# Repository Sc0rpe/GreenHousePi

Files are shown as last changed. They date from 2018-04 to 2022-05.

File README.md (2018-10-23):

# GreenHousePi
This Project is from four students of the [Technische Universität Bergakademie Freiberg](https://tu-freiberg.de) in germany.
It was created for the subject "application of information and automizationsystems".
The goal of this project is to build an autonomous greenhouse with different features using a raspberry pi.

Desired features:
* Tracking of Temperature, Humidity, Soil Moisture and Light Intensity
* Ability to open the roof for cooling and ventilation
* Turning on the lights if the available light intensity is too low
* Ventilate with the Fan if the humidity is too high
* Water if the soil moisture is too low
* Ability to be operated over a backend
* Displaying values over a LCD-Screen

# Installation
1. Download the latest raspbian image from https://www.raspberrypi.org/downloads/raspbian/
    (light image because of performance recommended)
2. Install it
3. Run
	`sudo raspi-config` 
    and enable the I2C Interface under advanced options
4. Dowload the ghpi-library, therefore run 
    `git clone https://github.com/Sc0rpe/GreenHousePi`
5. If you connected your devices on different pins than we did change the defines in the file
    `ghpi.cc` 
6. Go into the folder `ghpi` and run
    `make main`
    Output will be a file `ghpi.o`
7. You can run it with
    `sudo ./ghpi.o`
8. If you want it to start after boot automaticaly add
    `./path/to/ghpi.o`
    to the end of the file /etc/rc.local
9. Also you can copy the binary into the folder `/usr/local/bin` so you can run it from everywhere by typing `sudo ghpi.o`

# Setting up the Webinterface
1. Run 
    ```
    sudo apt-get update
    sudo apt-get upgrade
    ```
2. Install the `lighttpd` Webserver
    ```
    sudo apt-get install lighttpd
    ```
3. Install `php7.0`
    ```
    sudo apt-get install php7.0
    ```
4. Activate the FastCGI Modul for php and restart the server
    ```
    sudo lighty-enable-mod fastcgi
    sudo lighty-enable-mod fastcgi-php
    sudo service lighttpd force-reload
    ```
5. Add the user `www-data` to the sudoers so it can run the software modules.
    Therefore run `sudo visudo` and add the line `www-data ALL=(ALL) NOPASSWD: ALL` to it.
    Exit with `[CTRL] + [X]`, confirm with `[Y]` and press `[ENTER]`.
6. Go into the folder `GreenHousePi/ghpi/webscripts` and run:
    ```
    make
    sudo make install
    ```
    This will compile the modules and copy them, the html and php files into the root directory of the webserver. By default this is `/var/www/html` for lighttpd. If this is different for you, you have to copy them manually or change the concerning lines in the makefile.

# Class Layout
For the full UML class diagram please have a look at `Documentation/UML/GreenHousePi-ClassDiagram.png` or open the UML XML file on [Draw.io](https://draw.io)
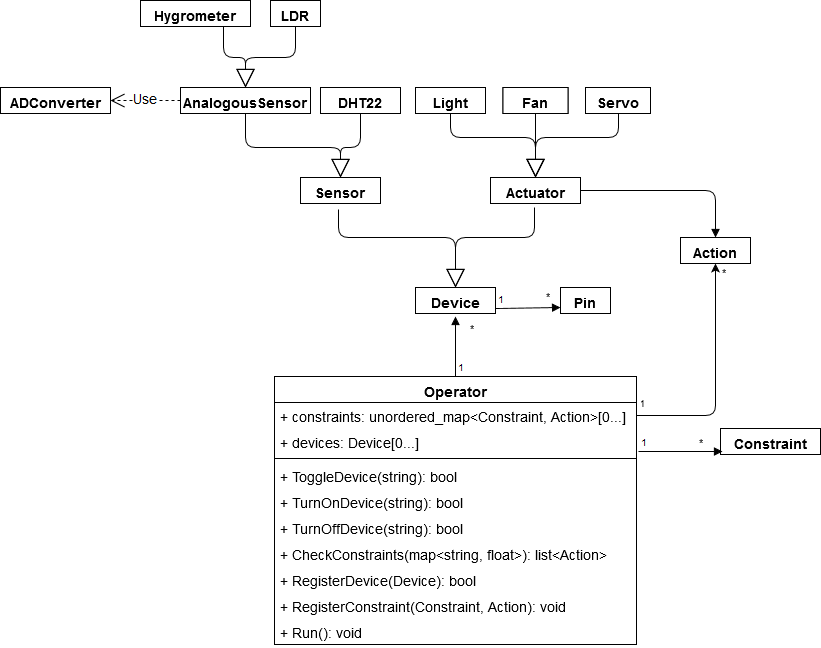
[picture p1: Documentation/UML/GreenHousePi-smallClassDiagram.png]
UML Class Diagram


# Cycle Schedule
This is what a cycle is doing. A cycle is one call of the Operater::Run function.
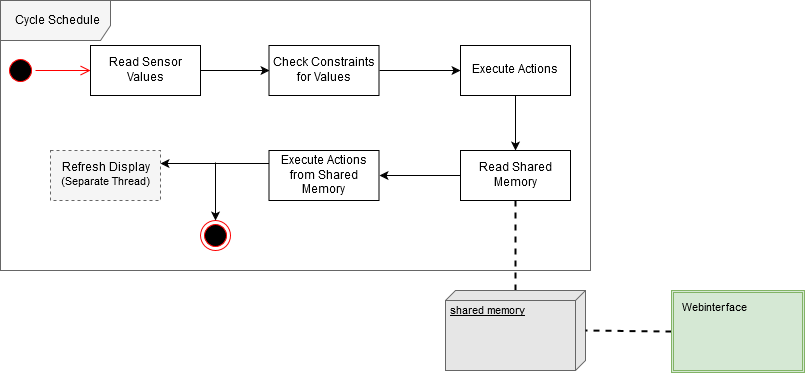
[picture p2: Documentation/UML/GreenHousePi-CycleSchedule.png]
Cycle schedule


# Adding your own Sensor
1. Create a new class and inherit from `ghpi::Sensor`
2. Override the `Run` and `get_values` function
4. Create an instance of your class, create some instances of Pin for your device and register them using the `RegisterPin()` function
5. Register your instance to the Operator using `RegisterDevice()`
6. For better understanding have look at the `dht22.cpp` file
7. Don't forget to add your newly created file to the makefile for the main target, otherwise it won't be linked if your run `make main`

# Adding your own Actuator
1. Create a new class and inherit from `ghpi::Actuator`
2. Override `TurnOn` `TurnOff` `Toggle` and if needed the `Run` function 
3. Create instances of `ghpi::Action` and register the actions your Actuator can execute by using `RegisterAction()`
4. Connect them by registering them with a Constraint on the operater using `RegisterConstraint`
5. Don't forget to add your newly created file to the makefile for the main target, otherwise it won't be linked if your run `make main`

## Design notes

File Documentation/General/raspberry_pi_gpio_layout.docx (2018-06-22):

Platine 3V | 3v3 | 5V | Platine 5V
Display SDA | 8 | 5V
Display SCL | 9 | GND
| 7 | 15
Platine GND | GND | 16 | RC2
LED_B | 0 | 1 | PWM
LED_G | 2 | GND
LED_R | 3 | 4 | RC3
| 3v3 | 5
ADC MOSI | 12 | GND | RC1
ADC MISO | 13 | 6 | DHT22 Data Pin
ADC CLK | 14 | 10 | ADC CS
Levelshifter GND | GND | 11

## GreenHousePi Pin Layout

Using wiringPi numbering!

RC stands for relay channel

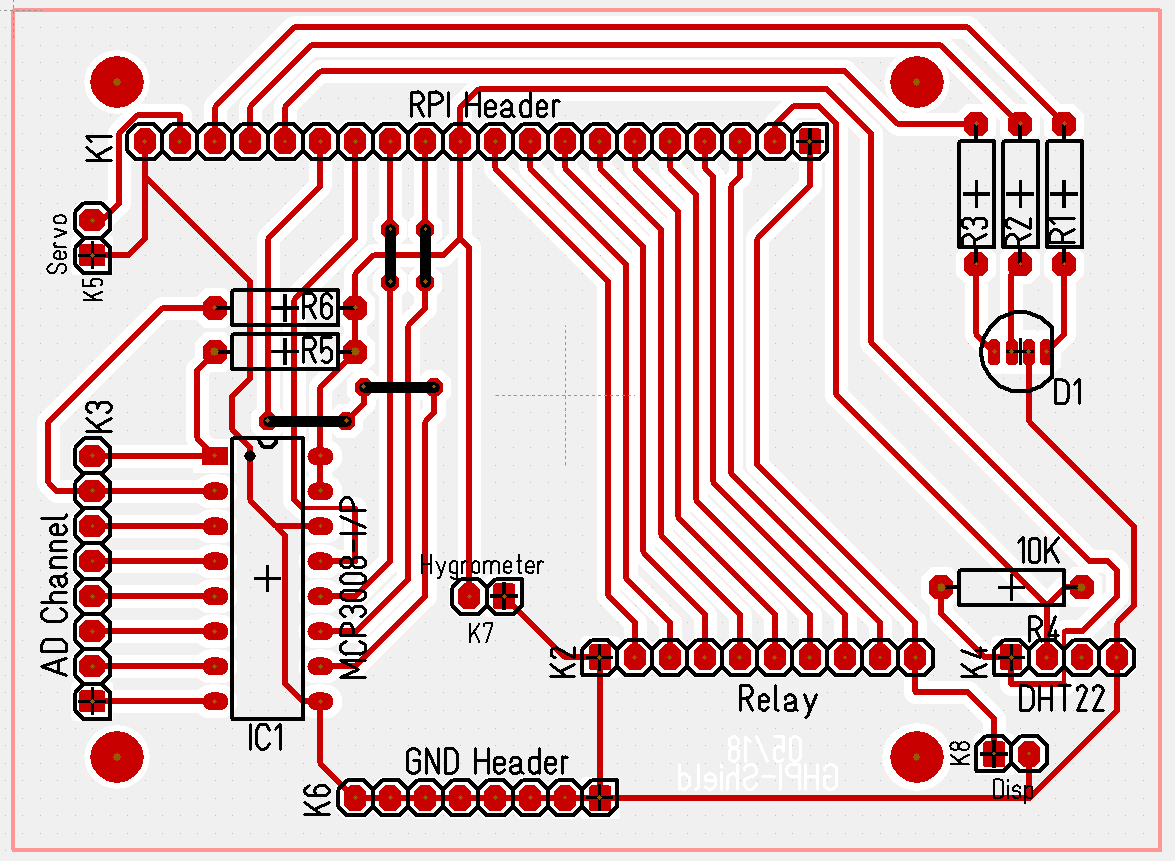
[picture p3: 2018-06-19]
Documentation/Images/ghpi_shield_pcb_layout_diagram.PNG

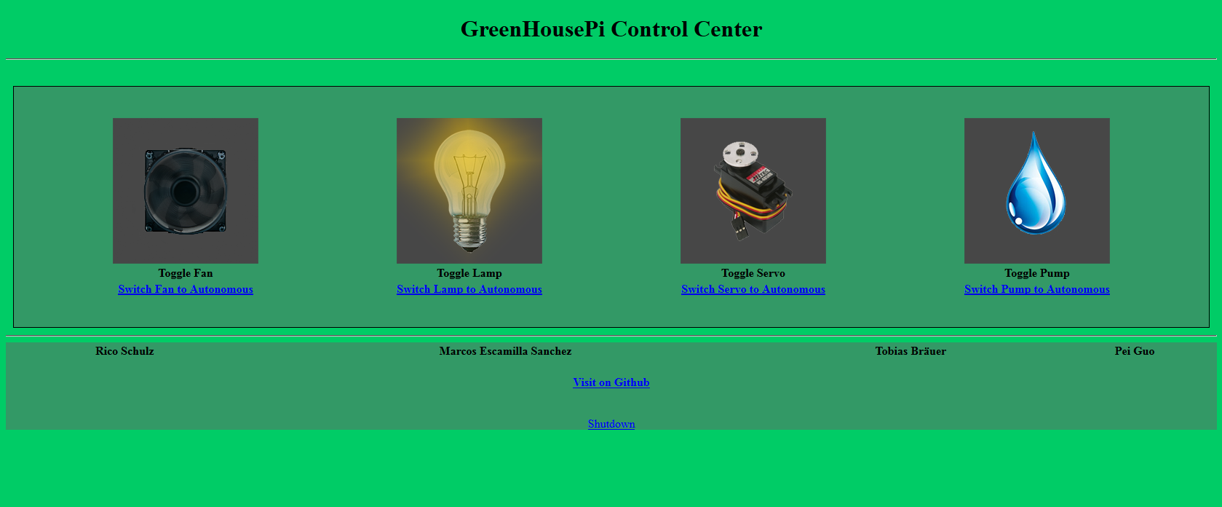
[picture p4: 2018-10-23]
Documentation/Images/webinterface.PNG

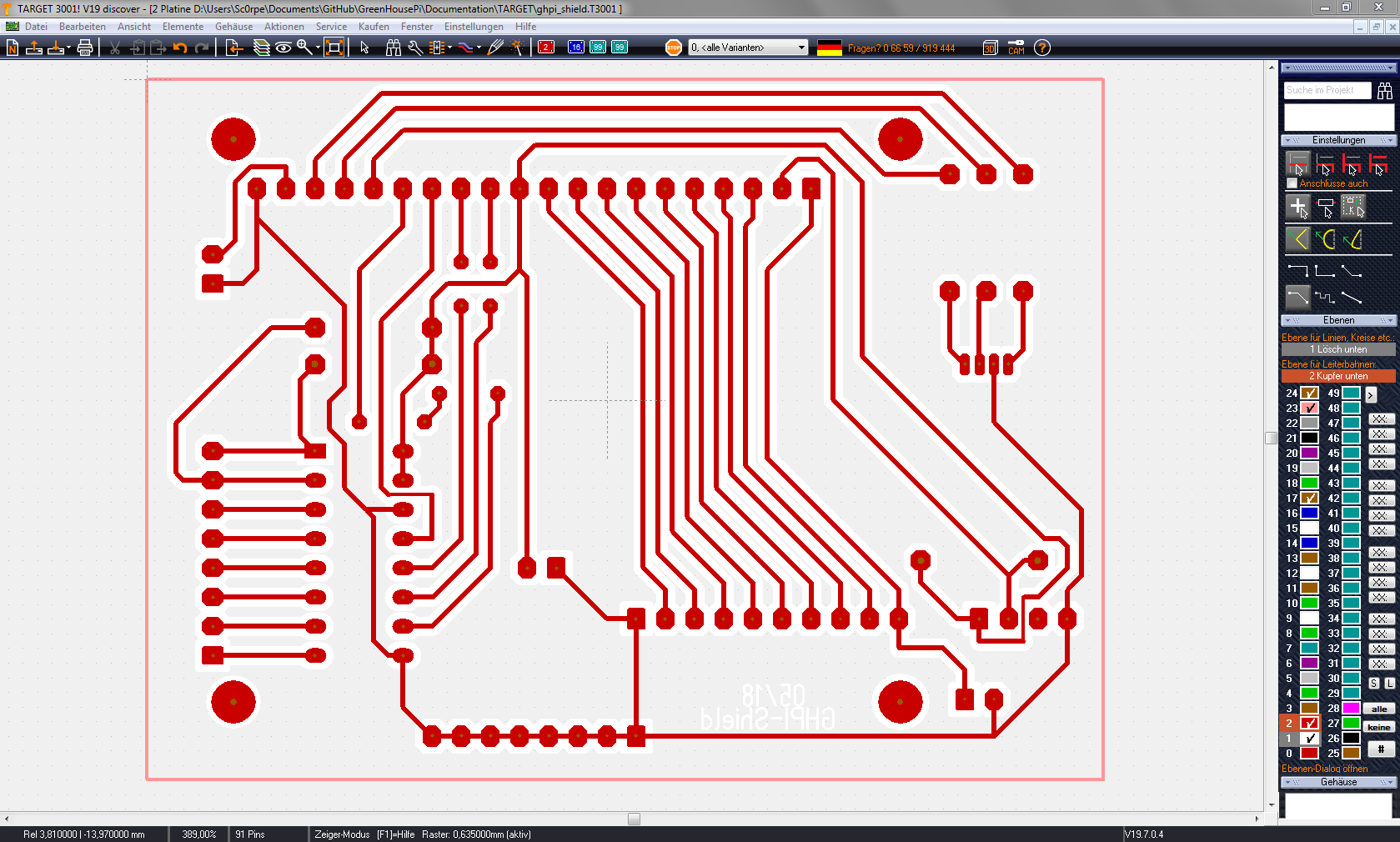
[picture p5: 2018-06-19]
Documentation/Images/target_screenshot1.PNG

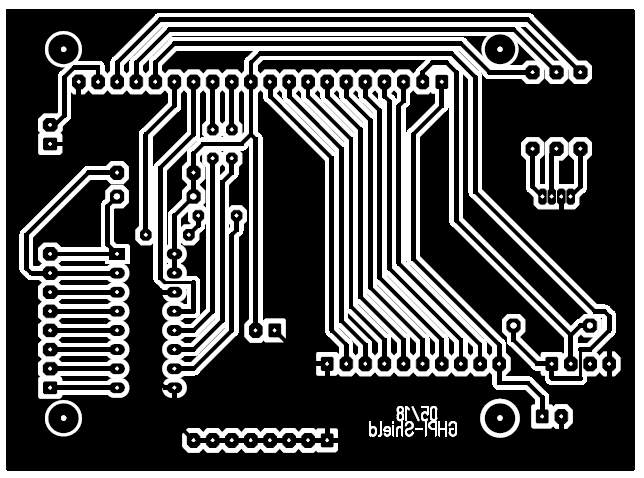
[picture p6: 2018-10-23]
Documentation/Images/illumination_mask.PNG

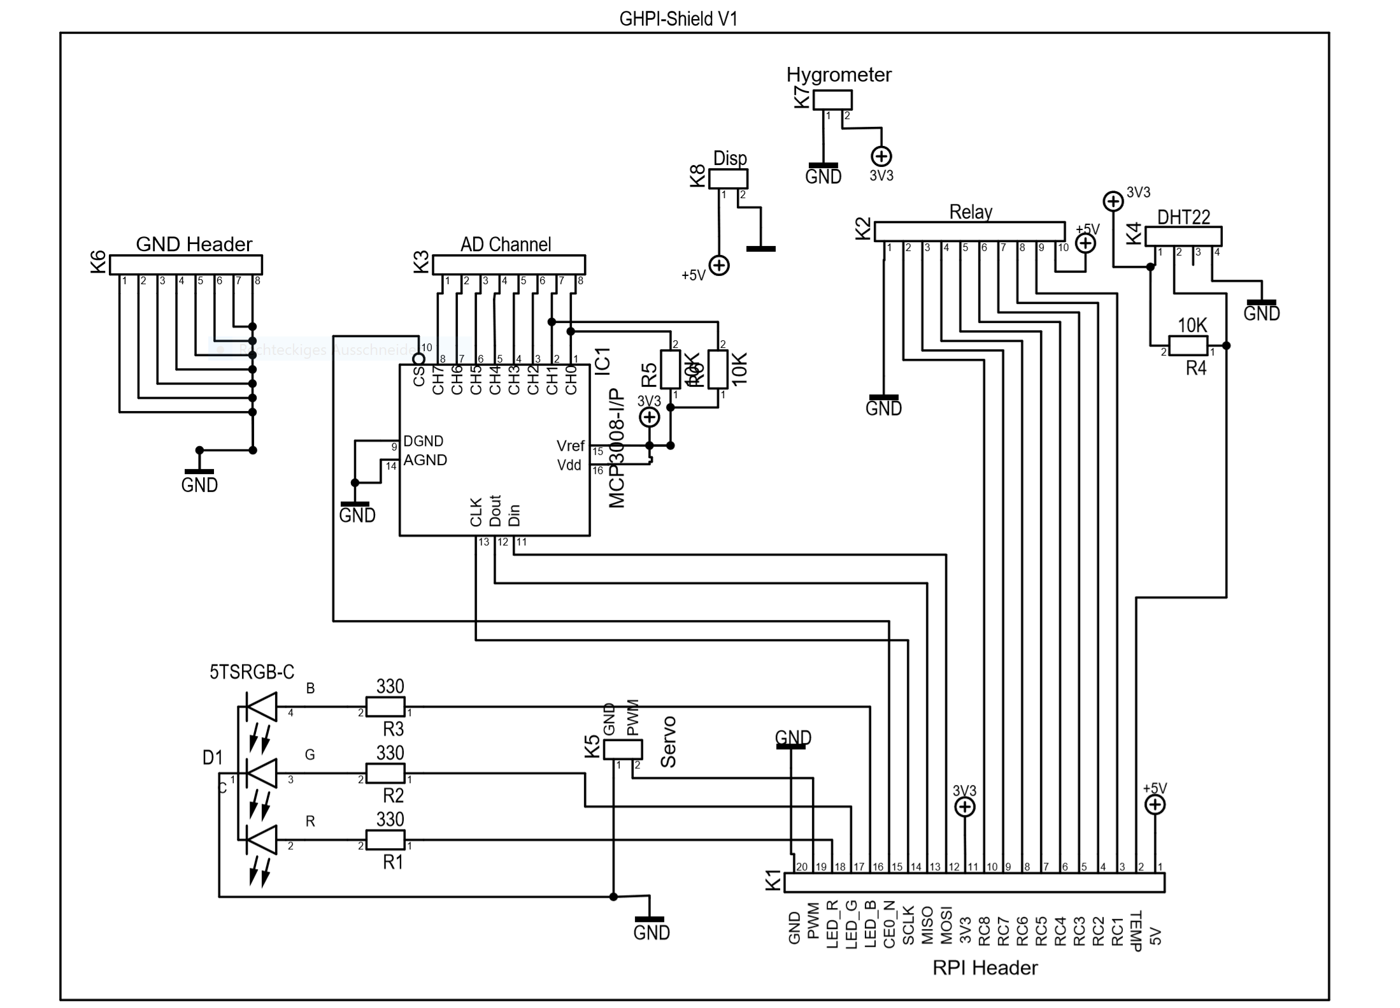
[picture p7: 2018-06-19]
Documentation/Images/ghpi_shield_sch.PNG

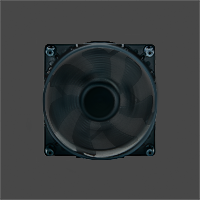
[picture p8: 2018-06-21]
ghpi/webscripts/images/fanON.png

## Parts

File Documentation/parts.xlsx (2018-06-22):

GreenHouse Pi Components
Component | Amount | Price per piece | Price
DHT22 Temperature and Humidity Sensor (https://www.amazon.de/AZDelivery-Temperatur-Luftfeuchtigkeitssensor-Arduino-Raspberry/dp/B06XF4TNT9) | 1 | 6.79 € | 6.79 €
Servo motor (https://www.amazon.de/Digital-Kuman-Rotating-Helicopter-Airplane/dp/B072V7RRF1?s=ce-de) | 1 | 19.29 € | 19.29 €
1000 uF Kondensator (https://www.amazon.de/Marken-100%C2%B5F-Kondensator-Elektrolytkondensator-Capacitor/dp/B014I7WV7A) | 1 | 0.58 € | 0.58 €
Raspberry Pi 2 Model B (https://www.amazon.de/Raspberry-Pi-quad-core-Cortex-A7-compatibility/dp/B00T2U7R7I?s=ce-de) | 0 | 37.99 € | 0.00 €
Power Supply for Motor (https://www.amazon.de/gp/product/B002E4WNWI/ref=oh_aui_detailpage_o00_s00?ie=UTF8&psc=1) | 1 | 12.00 € | 12.00 €
AD DA Wandler MCP3008 (https://www.amazon.de/gp/product/B005T6BA4K/ref=oh_aui_detailpage_o02_s00?ie=UTF8&psc=1) | 1 | 6.00 € | 6.00 €
8-Channel Relay (https://www.amazon.de/gp/product/B00AEIDWXK/ref=oh_aui_detailpage_o04_s00?ie=UTF8&psc=1) | 1 | 3.35 € | 3.35 €
photoconductive cell (https://www.amazon.de/gp/product/B00JGFF6HM/ref=oh_aui_detailpage_o04_s00?ie=UTF8&psc=1) | 2 | 0.18 € | 0.35 €
330 Ohm Resistor for the photoconductive cell | 3 | 0.00 € | 0.00 €
Power Supply Water pump 12V (https://www.amazon.de/Sunix-Netzadapter-100-240V-Transformatoren-Stromversorgung/dp/B074W2ZLDR) | 1 | 8.99 € | 8.99 €
Connector Strip (https://www.amazon.de/gp/product/B00GJP1JIM/ref=oh_aui_detailpage_o00_s00?ie=UTF8&psc=1) | 1 | 8.49 € | 8.49 €
Water Pump (https://www.amazon.de/TSSS-Wasserpumpe-Submersible-Gartenteich-Unterhaltung/dp/B01I9BN3CI) | 1 | 9.99 € | 9.99 €
Light (https://www.amazon.de/gp/product/B0183MDDZ0/ref=oh_aui_detailpage_o00_s00?ie=UTF8&psc=1) | 1 | 7.99 € | 7.99 €
Other stuff | 1 | 25.00 € | 25.00 €
Sum |  |  | 108.82 €
Price per Person |  |  | 27.20 €

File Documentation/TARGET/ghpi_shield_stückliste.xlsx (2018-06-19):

; Datum=09.Juni.2018 11:31
; Autor=Rico Schulz
Pos | Name | Wert | Gehäuse
1 | D1 | 5TSRGB-C | LED_5mm_RGB_4Pol
2 | IC1 | MCP3008-I/P | DIL16
3 | K1 | RPI Header | Stiftleiste_1x20_G_2,54
4 | K2 | Relay | Stiftleiste_1x10_G_2,54
5 | K3 | AD Channel | Stiftleiste_1x08_G_2,54
6 | K4 | DHT22 | Stiftleiste_1x04_G_2,54
7 | K5 | Servo | Stiftleiste_1x02_G_2,54
8 | K6 | GND Header | Stiftleiste_1x08_G_2,54
9 | K7 | Hygrometer | Stiftleiste_1x02_G_2,54
10 | K8 | Disp | Stiftleiste_1x02_G_2,54
11 | R1 | 330 Ohm | 0207_MET
12 | R2 | 330 Ohm | 0207_MET
13 | R3 | 330 Ohm | 0207_MET
14 | R4 | 10 kOhm | 0207_MET
15 | R5 | 10 kOhm | 0207_MET
16 | R6 | 10 kOhm | 0207_MET

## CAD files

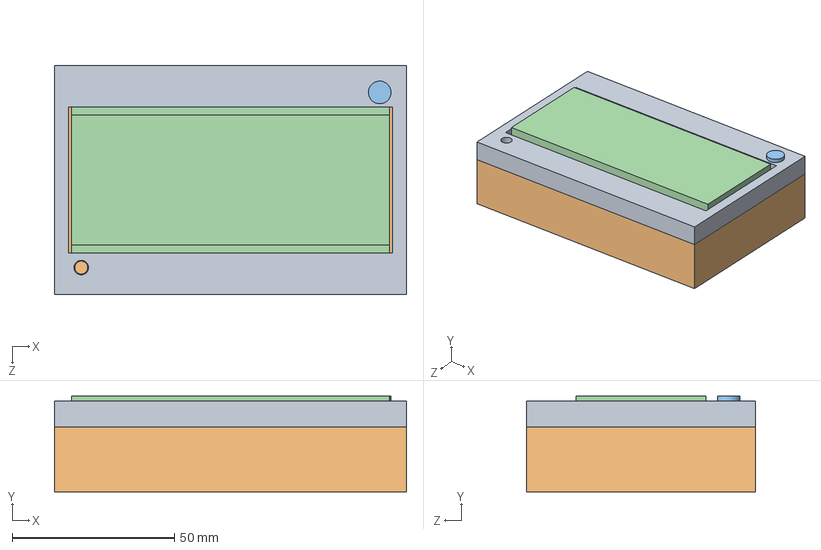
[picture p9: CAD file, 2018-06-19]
Documentation/SolidWorks CAD/Display/Displaycase.SLDASM
108.5 x 29.5 x 70.5 mm
Upper_case
Lower_case

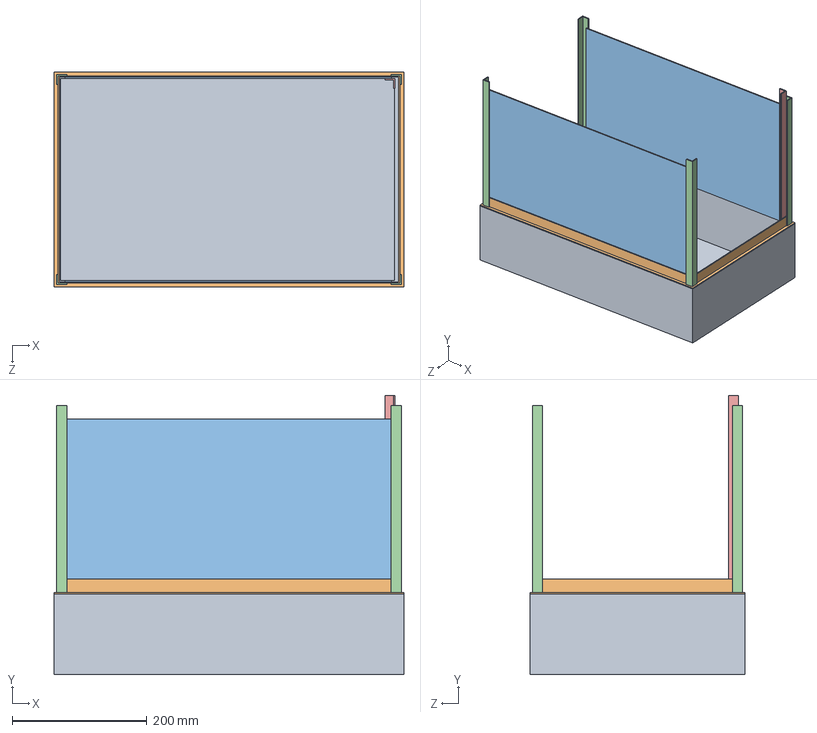
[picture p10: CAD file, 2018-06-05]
Documentation/SolidWorks CAD/Baugruppe.SLDASM
520.0 x 415.0 x 320.0 mm
bottom
bottom_frame
glass1 x 2
top_frame_out1 x 4
top_frame1

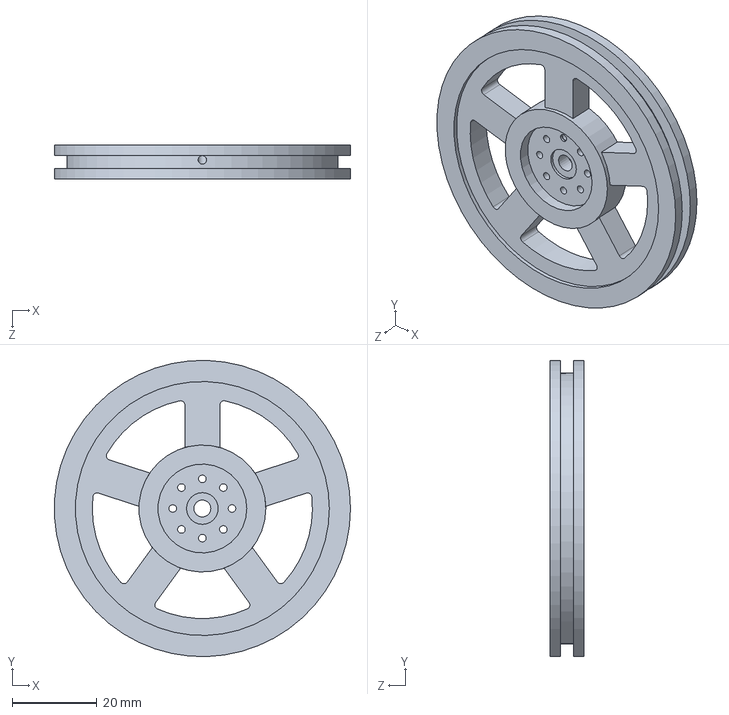
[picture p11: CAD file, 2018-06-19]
Documentation/SolidWorks CAD/Cable_Wheel/Cable_Wheel.SLDPRT
69.9 x 70.0 x 8.00 mm

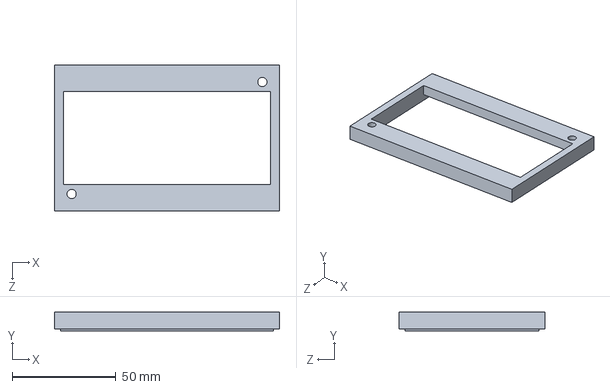
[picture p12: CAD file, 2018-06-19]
Documentation/SolidWorks CAD/Display/3D-Print/Upper_case.SLDPRT
108.5 x 9.00 x 70.5 mm

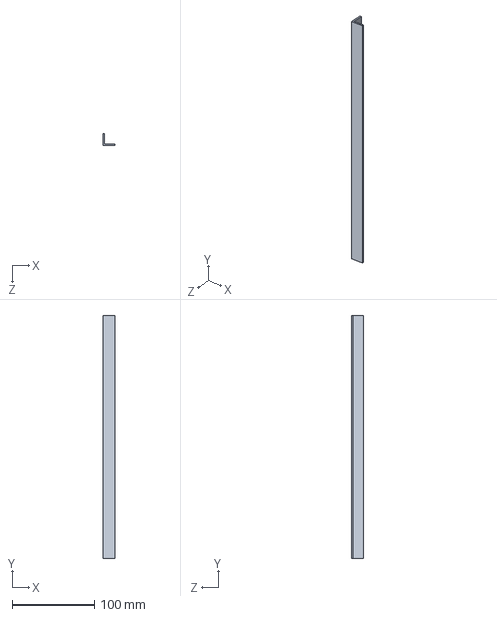
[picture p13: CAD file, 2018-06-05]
Documentation/SolidWorks CAD/top_frame1.SLDPRT
15.0 x 295.0 x 15.0 mm

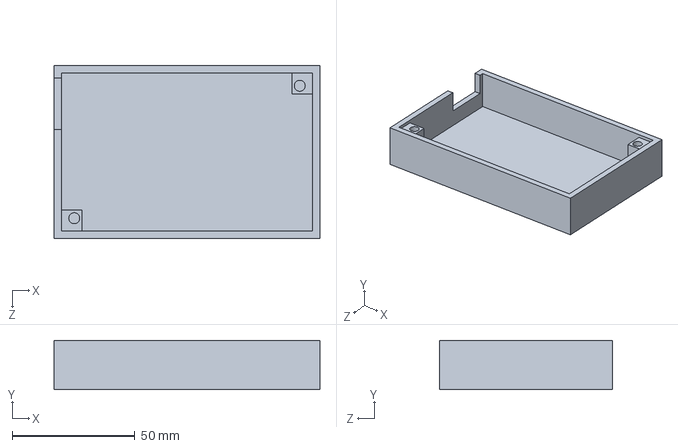
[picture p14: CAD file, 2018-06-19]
Documentation/SolidWorks CAD/Display/3D-Print/Lower_case.SLDPRT
108.5 x 20.0 x 70.5 mm

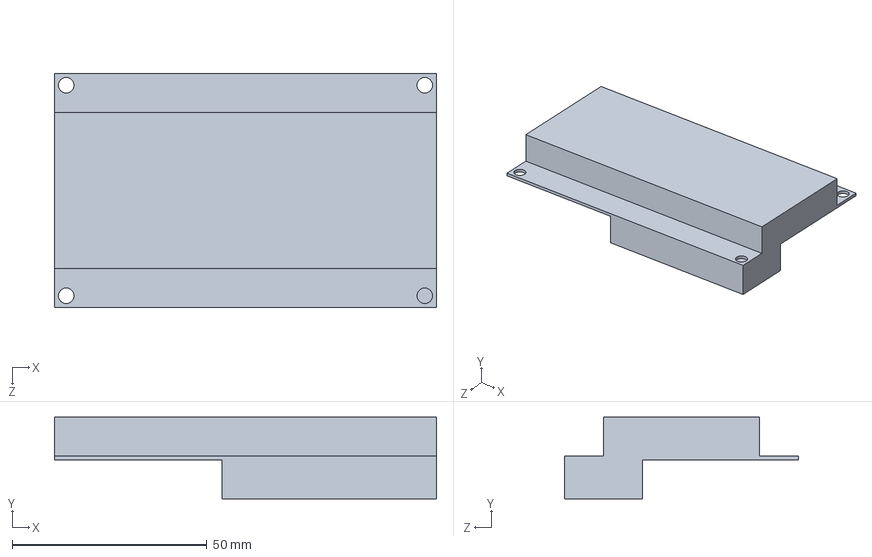
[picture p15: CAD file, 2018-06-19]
Documentation/SolidWorks CAD/Display/Display.SLDPRT
98.0 x 21.0 x 60.0 mm

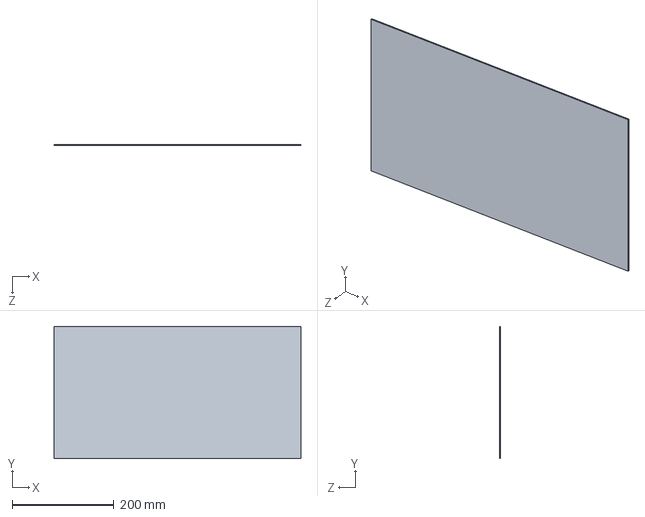
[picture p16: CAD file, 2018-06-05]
Documentation/SolidWorks CAD/glass1.SLDPRT
485.0 x 260.0 x 2.00 mm

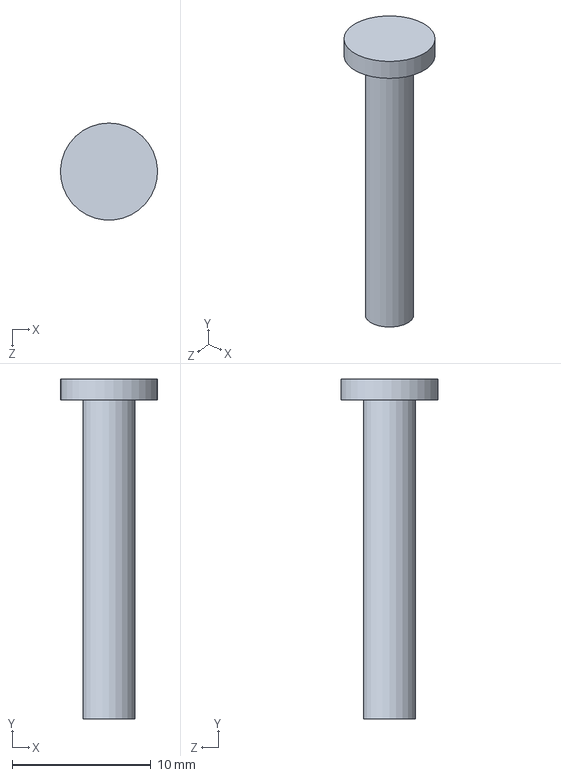
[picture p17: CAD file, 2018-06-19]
Documentation/SolidWorks CAD/Display/3D-Print/case_pin.SLDPRT
6.99 x 24.5 x 6.98 mm

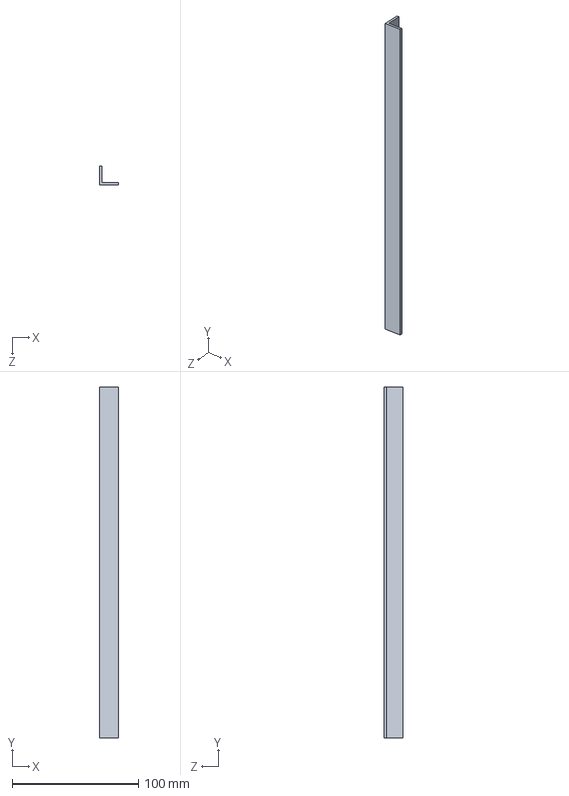
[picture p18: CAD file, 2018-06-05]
Documentation/SolidWorks CAD/top_frame_out1.SLDPRT
15.0 x 278.0 x 15.0 mm

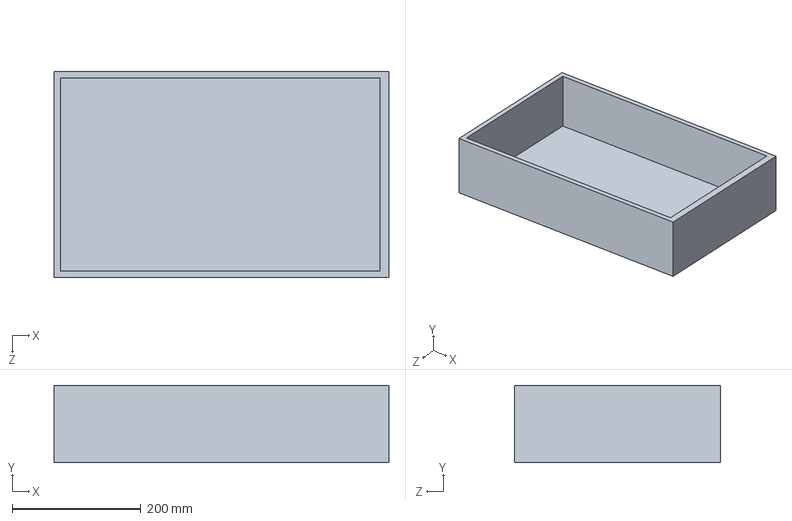
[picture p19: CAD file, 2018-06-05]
Documentation/SolidWorks CAD/bottom.SLDPRT
520.0 x 120.0 x 320.0 mm

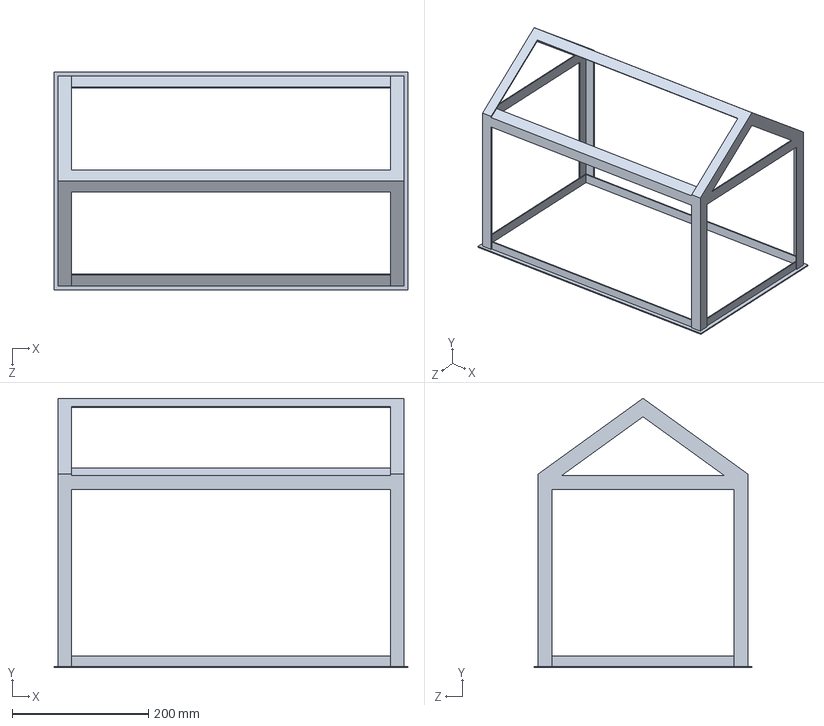
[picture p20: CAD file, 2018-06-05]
Documentation/SolidWorks CAD/top.SLDPRT
520.0 x 395.8 x 320.0 mm

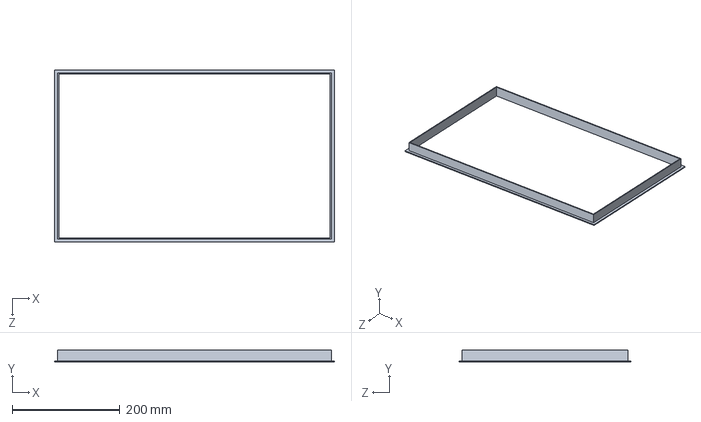
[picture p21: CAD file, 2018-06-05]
Documentation/SolidWorks CAD/bottom_frame.SLDPRT
520.0 x 22.0 x 320.0 mm

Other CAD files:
Documentation/SolidWorks CAD/Cable_Wheel/Cable_Wheel.STL
Documentation/SolidWorks CAD/Display/3D-Print/Lower_case.STL
Documentation/SolidWorks CAD/Display/3D-Print/Upper_case.STL
Documentation/SolidWorks CAD/Display/3D-Print/case_pin.STL
Documentation/SolidWorks CAD/greenhousepi_sketch.SLDDRW

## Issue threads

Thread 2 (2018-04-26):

Used GPIO Pins are not exportet on startup

Sc0rpe, 2018-04-26:
GPIOs are first exportet when the script wants to use it. This leads to a not working backend. If a device for instance the fan was not used by the script yet the backend functions will not switch its status.

Sc0rpe, 2018-04-30:
added pin_exporter.cpp
Let this be called after startup. Put this in /etc/rc.local to do this.
Not yet tested!

Sc0rpe, 2018-05-04:
Tested. Is working!

Closed 2018-05-04.

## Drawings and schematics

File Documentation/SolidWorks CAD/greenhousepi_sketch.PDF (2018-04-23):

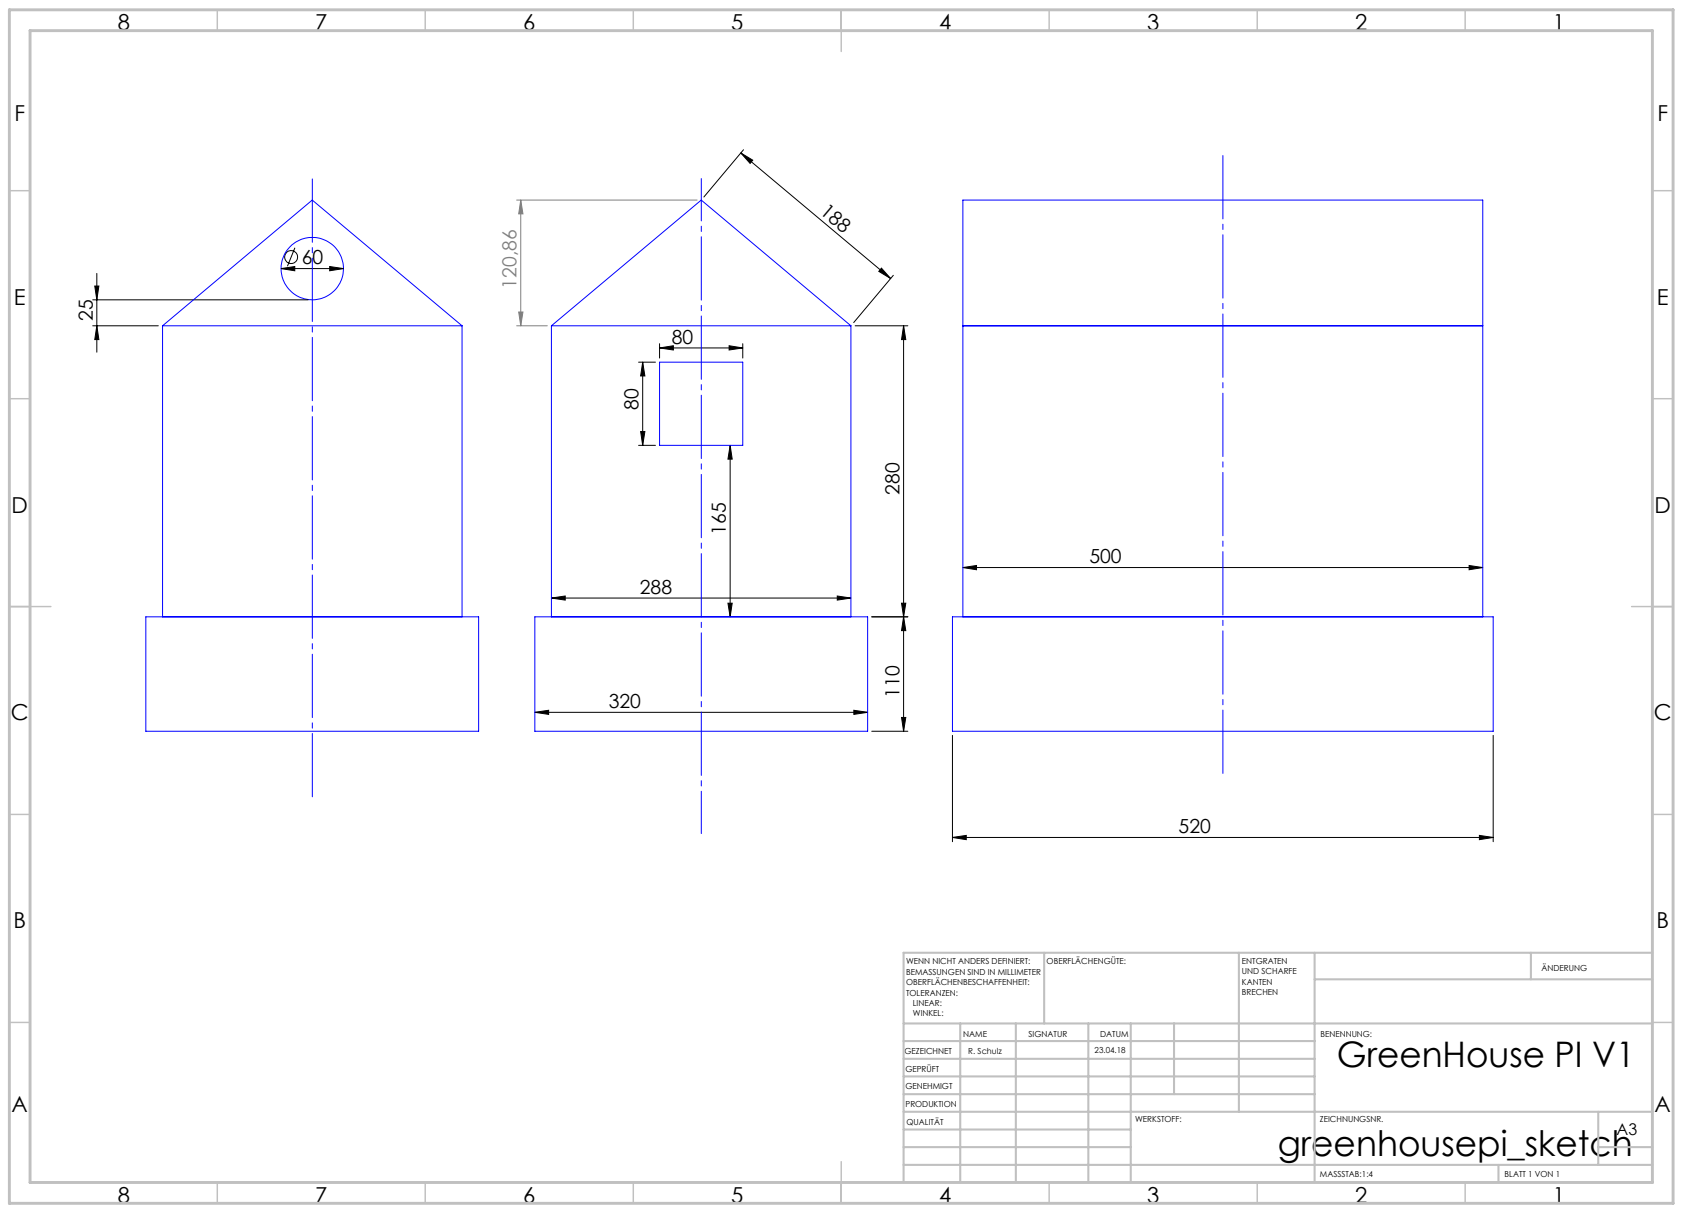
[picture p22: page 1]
MASSSTAB:1:4; BLATT 1 VON 1; UND SCHARFE; WENN NICHT ANDERS DEFINIERT:; OBERFLÄCHENGÜTE:

BEMASSUNGEN SIND IN MILLIMETER
OBERFLÄCHENBESCHAFFENHEIT:
TOLERANZEN:
LINEAR:
WINKEL:

NAME | SIGNATUR | DATUM | | | | BENENNUNG: GreenHouse PI V1
QUALITÄT | | | | WERKSTOFF: greenhousepi_sketch | ZEICHNUNGSNR. | A3

GEZEICHNET | R. Schulz | | 23.04.18
GEPRÜFT
GENEHMIGT
PRODUKTION

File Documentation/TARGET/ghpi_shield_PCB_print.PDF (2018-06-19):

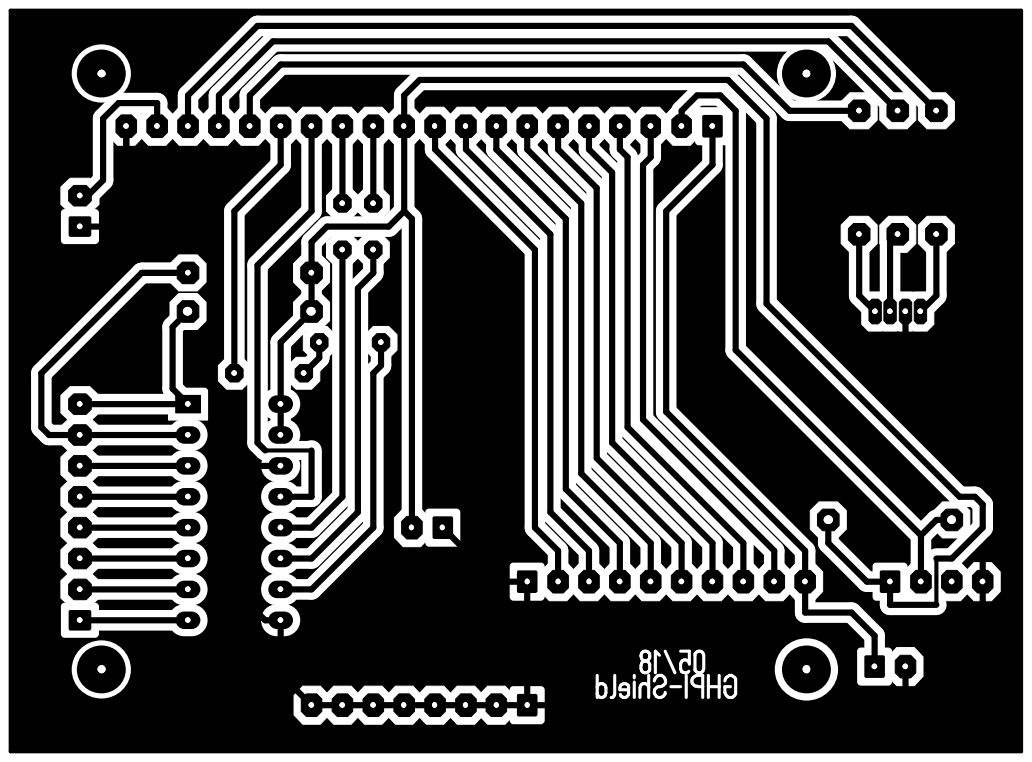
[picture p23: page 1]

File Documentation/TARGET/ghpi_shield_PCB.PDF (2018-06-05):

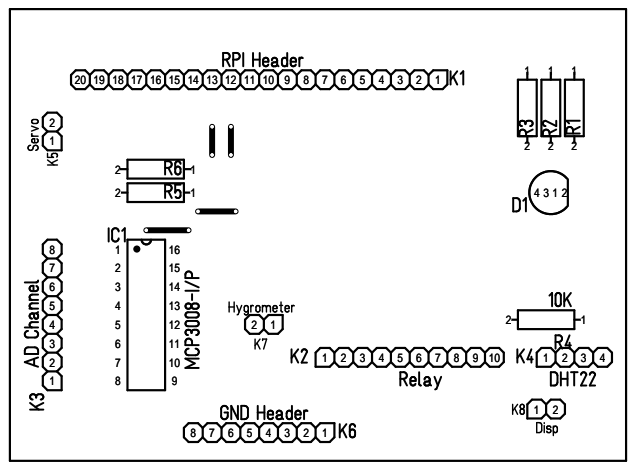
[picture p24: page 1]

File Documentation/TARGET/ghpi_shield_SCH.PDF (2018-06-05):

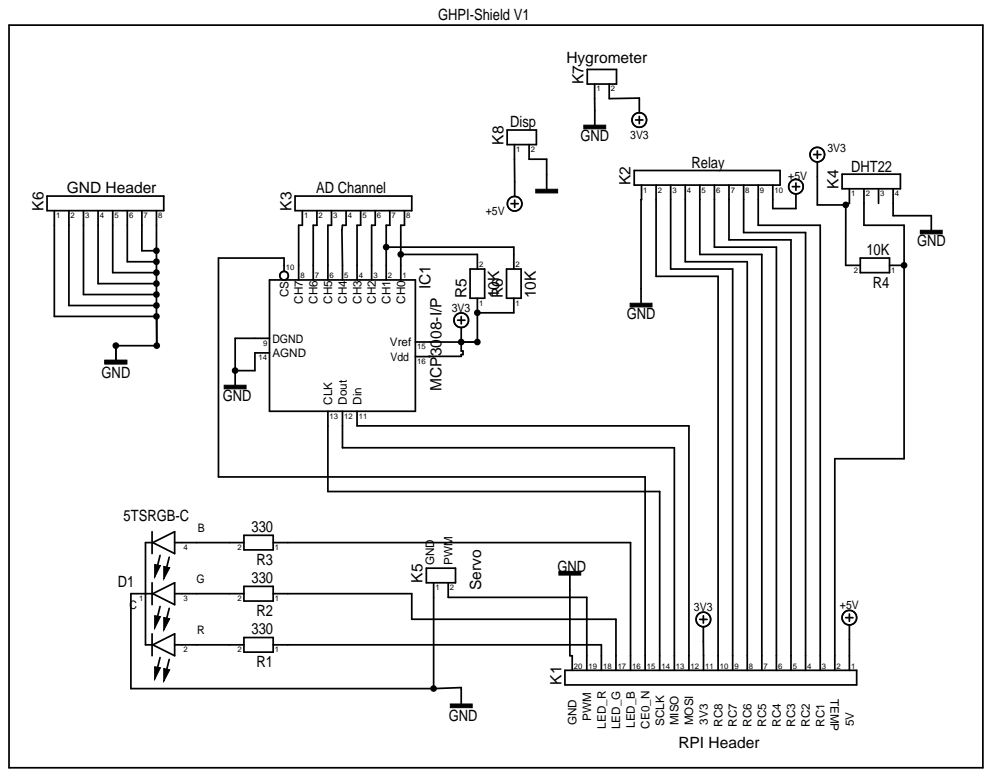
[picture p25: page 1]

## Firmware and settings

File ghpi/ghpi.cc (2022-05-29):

//
// 2018 Rico Schulz
//
#pragma once
#include <iostream>
#include <cstdlib>
#include <csignal>
#include <boost/log/trivial.hpp>
#include "operator.h"
#include "dht22.h"
#include "ldr.h"
#include "hygrometer.h"
#include "servo.h"
#include "pump.h"
#include "debug.h"


#ifdef DEBUG
#define SERVO_PIN 1
#define DHT_PIN 6
#define HYGRO_PIN 42
#define PUMP_PIN 42
#define LAMP_PIN 16
#define FAN_PIN 5
#define INTERVALL 10000
#endif

using namespace ghpi;

bool STOP = false;

// Set STOP to true, so we will break
// out of the infinite loop and exit the main function
// this will call the destructors of our object and the pins will
// set to their default init state
void exiting(int i) {
	STOP = true;
}

int main() {
  
    wiringPiSetup();
    Operator ghoperator;
    
    signal(SIGABRT, exiting);
    signal(SIGTERM, exiting);
    //signal(SIGTSTP, exiting);
    signal(SIGINT, exiting);	
    
    // Instantiate some devices for testing
    DHT22 dht;
    ADConverter adcon(14, 12, 13, 10, 0, 1023);
    Hygrometer hygro(&adcon, 7);
    LDR ldr1(&adcon, 0);
    LDR ldr2(&adcon, 1);
    Servo servo(270, 0);
    Pump pump;
    Actuator lamp("Lamp");
    Actuator fan("Fan");
    LCDDisplay* lcd = nullptr;
      
    try {
      // Write welcome screen to display
      lcd = new LCDDisplay();
      lcd->writeLine("GreenHousePi V1.0", 1);
      lcd->writeLine("Made by", 2);
      lcd->writeLine(" Tobi          Pei ", 3);
      lcd->writeLine(" Rico        Marcos", 4);
    }
    catch (...) {
      std::cout << "LCD has thrown an error" << std::endl;
    }
      
    ghoperator.Set_LCDDisplay(lcd);
      
    Pin dht_data_pin(DHT_PIN, PinMode::input, PinState::low);
    Pin hygro_pin(HYGRO_PIN, PinMode::output, PinState::high);
    Pin servo_pin(SERVO_PIN, PinMode::pwmoutput, PinState::low);
    Pin pump_pin(PUMP_PIN, PinMode::output, PinState::high);
    Pin lamp_pin(LAMP_PIN, PinMode::output, PinState::high);
    Pin fan_pin(FAN_PIN, PinMode::output, PinState::high);
      
      
    // Register pins for the devices
    dht.RegisterPin(&dht_data_pin, PinUsage::BI_DATA, OnState::OS_NONE);
    hygro.RegisterPin(&hygro_pin, PinUsage::SWITCH, OnState::OS_LOW);
    servo.RegisterPin(&servo_pin, PinUsage::PWM, OnState::OS_NONE);
    pump.RegisterPin(&pump_pin, PinUsage::SWITCH, OnState::OS_LOW);
    lamp.RegisterPin(&lamp_pin, PinUsage::SWITCH, OnState::OS_LOW);
    fan.RegisterPin(&fan_pin, PinUsage::SWITCH, OnState::OS_LOW);
      
    // Register Devices
    ghoperator.RegisterDevice(&dht);
    ghoperator.RegisterDevice(&hygro);
    ghoperator.RegisterDevice(&servo);
    ghoperator.RegisterDevice(&pump);
    ghoperator.RegisterDevice(&ldr1);
    ghoperator.RegisterDevice(&ldr2);
    ghoperator.RegisterDevice(&lamp);
    ghoperator.RegisterDevice(&fan);

    // Creating Constraints
    Constraint temp("TempBelow18°C", EnvironmentValueStrings[EnvironmentValue::TEMPERATURE],
                      18.f, ConstraintConditionStrings[ConstraintCondition::BELOW]);
    Constraint hum("HumBelow80%", EnvironmentValueStrings[EnvironmentValue::HUMIDITY],
                      80.f, ConstraintConditionStrings[ConstraintCondition::BELOW]);
    Constraint lightlow("LightIntOver300", EnvironmentValueStrings[EnvironmentValue::LIGHT_INTENSITY],
                      300.f, ConstraintConditionStrings[ConstraintCondition::OVER]);
    Constraint lighthigh("LightIntUnder500", EnvironmentValueStrings[EnvironmentValue::LIGHT_INTENSITY],
                      500.f, ConstraintConditionStrings[ConstraintCondition::BELOW]); 
                        
    // Creating Actions for Devices
    Action open_roof("OpenRoof", ActionFn::AFN_ON, NULL);
    Action close_roof("CloseRoof", ActionFn::AFN_OFF, NULL);
    Action turn_on_light("TurnOnLight", ActionFn::AFN_ON, NULL);
    Action turn_off_light("TurnOffLight", ActionFn::AFN_OFF, NULL);
    Action turn_on_fan("TurnOnFan", ActionFn::AFN_ON, NULL);
    Action toggle_servo("ToggleServo", ActionFn::AFN_TOGGLE, NULL);
    Action toggle_lamp("ToggleLamp", ActionFn::AFN_TOGGLE, NULL);
    Action toggle_fan("ToggleFan", ActionFn::AFN_TOGGLE, NULL);
		Action op_man("OperateManually", ActionFn::AFN_OP_MANU, NULL);
		Action op_auto("OperateAutonomous", ActionFn::AFN_OP_AUTO, NULL);
      
    // Register Actions on devices
    servo.RegisterAction(open_roof);
    servo.RegisterAction(close_roof);
    servo.RegisterAction(toggle_servo);
    fan.RegisterAction(turn_on_fan);
    fan.RegisterAction(toggle_fan);
    lamp.RegisterAction(turn_off_light);
    lamp.RegisterAction(turn_on_light);
    lamp.RegisterAction(toggle_lamp);
		servo.RegisterAction(op_man);
		lamp.RegisterAction(op_man);
		fan.RegisterAction(op_man);
		servo.RegisterAction(op_auto);
		lamp.RegisterAction(op_auto);
		fan.RegisterAction(op_auto);
      
    // Register Constraints
    ghoperator.RegisterConstraint(temp, open_roof);
    ghoperator.RegisterConstraint(hum, turn_on_fan);
    ghoperator.RegisterConstraint(lightlow, turn_on_light);
    ghoperator.RegisterConstraint(lighthigh, turn_off_light);

    // Initialize Devices
    servo.Initialize();
      
    ghoperator.PrintDevices();
    ghoperator.PrintConstraints();
    std::cout << "Start running operator" << std::endl;
    std::cout << "Running in intervalls of " << INTERVALL << " milliseconds" << std::endl;
      
    while (!STOP) {
      ghoperator.Run();
      delay(INTERVALL);
    }
    std::cout << "Exiting..." << std::endl;
    lcd->ClrLcd();
    lcd->writeLine("Goodbye...", 2);
    delay(2000);
    lcd->ClrLcd();
    delete lcd;
  
    
    return 0;
}

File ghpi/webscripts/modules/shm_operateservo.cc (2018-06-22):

//
// 2018 Rico Schulz
//
#pragma once
#include <vector>
#include <iostream>
#include <boost/interprocess/shared_memory_object.hpp>
#include <boost/interprocess/mapped_region.hpp>
#include <boost/interprocess/sync/interprocess_mutex.hpp>
#include <boost/interprocess/sync/scoped_lock.hpp>
#include "operator.h"
#include "action.h"

using namespace boost::interprocess;

int main() {
  boost::interprocess::shared_memory_object shm_messages_;
  boost::interprocess::mapped_region region_;
  
  shm_messages_ = shared_memory_object(open_only, ghpi::Operator::SHM_NAME, read_write);
  shm_messages_.truncate(sizeof(ghpi::Operator::MSGQueue));
  region_ = mapped_region(shm_messages_, read_write);
  
  //Get the address of the mapped region
  void * addr       = region_.get_address();
  //Construct the shared structure in memory
  ghpi::Operator::MSGQueue * data = static_cast<ghpi::Operator::MSGQueue*>(addr);
  
  ghpi::Action op_auto_servo("OperateAutonomous", ghpi::ActionFn::AFN_OP_AUTO, NULL, "Servo_5", true);
  { // Code block for scoped_lock. Mutex will automatically unlock after block.
    // even if an exception occurs
    scoped_lock<interprocess_mutex> lock(data->mutex);
    
    // Put the action in the shared memory object
		data->Put(op_auto_servo);
  }
  
  std::cout << "Added Action " << op_auto_servo.get_name() << " to queue" << std::endl;
  
  return 0;
}

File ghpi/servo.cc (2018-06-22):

//
// 2018 Rico Schulz
//
#pragma once
#include "servo.h"

using ghpi::Servo;

void Servo::Initialize() {
    // Set the motor position to initial one
    SetUpPWM();
    SetPosition(angle_);
}

void Servo::TurnOn() {
  // Set Servo Position to max angle
  SetPosition(SERVO_ON_POS);
	state_ = ghpi::DeviceState::ON;
}

void Servo::TurnOff() {
  // Set Servo Position to min angle
  SetPosition(SERVO_OFF_POS);
	state_ = ghpi::DeviceState::OFF;
}

void Servo::SetUpPWM() {
  pwmSetMode(PWM_MODE_MS);
  
  pwmSetClock(GHPI_PWM_CLOCK);
  pwmSetRange(GHPI_PWM_RANGE);
}

int Servo::get_angle() {
  return angle_;
}

int Servo::ConvertAngleToValue(int angle) {
  float value;
  value = angle * (1.f/135.f) + 1.5f; // This gives us the time in ms for the angle
  value = value * (float)((19200000.f/(GHPI_PWM_CLOCK * GHPI_PWM_RANGE))); // Convert to value
  return (int)value;
}

void Servo::SetPosition(int angle) {  
  const int stepdelay = 40;
  
  // Do not kill the servo with impossible angles
  if (angle > 135 || angle < -135) {
    return;
  }
  
  // Get PWM Pin for Servo
  int pwm_pin = GetPinsByUsage(ghpi::PinUsage::PWM).at(0)->get_number();
  
  // Adapt stepwise to the desired angle 
  if (angle > angle_) {
    for (int step = angle_; step < angle; ++step) {
      pwmWrite(pwm_pin, ConvertAngleToValue(step));
      delay(stepdelay);
      angle_ = step;
    }
  } else {
    for (int step = angle_; step > angle; --step) {
      pwmWrite(pwm_pin, ConvertAngleToValue(step));
      delay(stepdelay);
      angle_ = step;
    }
  }
}

Servo::Servo(int max_angle, int init_angle) : Actuator() {
  name_ = "Servo_" + std::to_string(get_count());
  max_angle_ = max_angle;
  angle_ = init_angle;
}

Servo::~Servo() {
  SetPosition(SERVO_OFF_POS);
	delay(200);
}

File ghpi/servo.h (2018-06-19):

//
// 2018 Rico Schulz
//
#pragma once
#include "actuator.h"

#define GHPI_PWM_CLOCK 384
#define  GHPI_PWM_RANGE 1000

#define SERVO_OFF_POS 0
#define SERVO_ON_POS -130

namespace ghpi {
  
  // Class for the Kuman KY72 Servo
  class Servo : public Actuator {
   public:
    void TurnOn() override;
    void TurnOff() override;
    int get_angle();
    void Initialize();
    Servo(int max_angle, int init_angle);
    ~Servo();
    
   private:
    // Functions
    void SetUpPWM();
    void SetPosition(int angle);
    
    // Converts an angle to corresponding value for PWM.
    // Function assumes 50Hz and a PWM Range of 1000.
    // 0° is the neutral position of the motor
    // Angle is evenly spreaded around the neutral position.
    //  ARGS:
    //    angle: angle the motor should be steered to
    // RETURNS:
    //    The corresponding value for the PWM
    int ConvertAngleToValue(int angle);
    
    // Data Member
    // Angle the motor can totaly rotate
    int max_angle_;
    
    // Current angle of the motor
    int angle_;
   
  };
};

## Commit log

2018-04-23 Added Documentation, Datasheets and excel file for parts
    [parts.xlsx]
2018-04-26 updated parts.xlsx
    [parts.xlsx]
2018-04-30 added pin_exporter, more comments, little adjusments
    pin exporter will export the pins for our devices at startup.
2018-05-01 little fix for the pin-exporter script
2018-05-01 added fritzing schematic
    [wiring_schematic_pcb.fzz]
2018-05-04 updated parts and schematic
    [parts.xlsx, wiring_schematic_pcb.fzz]
2018-05-09 added servo variables
2018-05-14 added some more comments again. Added Servotest programm
2018-05-20 fixed servotest
2018-05-20 updated servotest
2018-05-24 added RGB LED data sheets and RGB LED to fritzing schematic
    [wiring_schematic_pcb2.fzz]
2018-05-25 big update of ghpi library
    added servo class
    fixed servotest.cpp
    some other new functions
    [Servotest.cpp, dht22.cc, servo.cc]
2018-05-27 ghpi library update, new pcb schematic
    [parts.xlsx]
2018-05-28 updated PCB
2018-05-28 update schematic
2018-05-29 finalized ghpi shield pcb
2018-06-05 added circuit diagram and layout diagram
2018-06-05 added SolidWorks files for the greenhouse model
    [Baugruppe.SLDASM, bottom.SLDPRT, bottom_frame.SLDPRT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]
2018-06-05 SolidWorks und STL Modell der Riemenscheibe
    Riemenscheibe
    [Cable_Wheel.SLDPRT, Cable_Wheel.STL]
2018-06-07 now possible to set the motor to a specific angle
2018-06-11 removed unnecessary files
    [Cable_Wheel.SLDPRT, Cable_Wheel.STL]
2018-06-11 more documentation files
    target interface screenshot
    greenhousepi scetch
    ghpi shiled PCB printable PDF
    parts list for ghpi shield PCB
    [ghpi_shield_stückliste.xlsx]
2018-06-12 fixed everything so it is now compiling
    [adconverter.cc]
2018-06-14 fixed some bugs and tested a little bit
    just before the first release now :)
    [adconverter.cc]
2018-06-16 pins have now an init function
    Init function exports the pin and writes the initial state of the pin
2018-06-16 Corrected some stupid mistakes in the display-classes ... sorry :s
    [lcddisplay.cc]
2018-06-17 Corrected stupid #define mistake .. I'm terribly sorry :(
    [lcddisplay.cc]
2018-06-18 little fixes and integration of lcd
    [dht22.cc, ghpi.cc, lcddisplay.cc]
2018-06-18 Servo is now adapting "slowly" to the desired angle in SetPosition
2018-06-18 bugfix with servo initialization
    [ghpi.cc, servo.cc]
2018-06-19 Documentation updated
    removed unused files
    added gpio header layout
    added some png files for the presentation
    edited list of parts
    [ghpi_shield_stückliste.xlsx, parts.xlsx]
2018-06-19 3D-Print data for display case
    [Cable_Wheel.SLDPRT, Display.SLDPRT, Displaycase.SLDASM]
2018-06-22 big update
    Targets for actions,
    support for autonomous and manually operated devices,
    new files for webinterface
